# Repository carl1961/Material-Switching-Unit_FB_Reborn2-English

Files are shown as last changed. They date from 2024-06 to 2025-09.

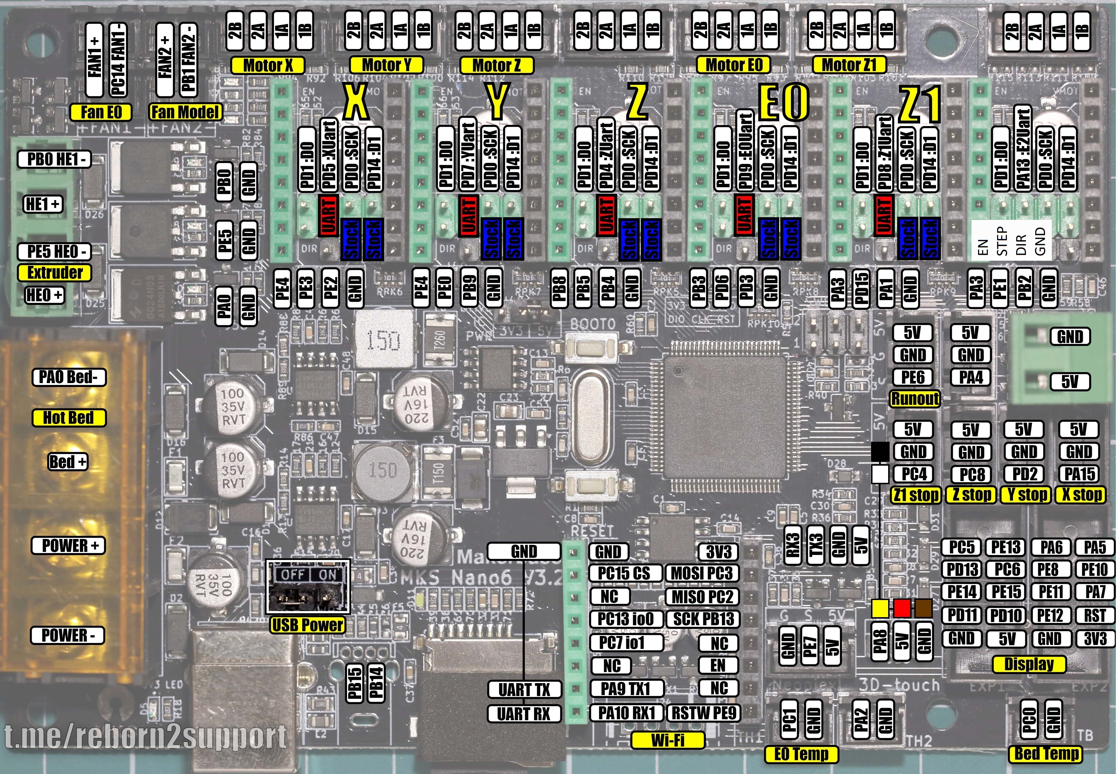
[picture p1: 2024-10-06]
MKS_Nano6_v3.2_PINOUT.jpg

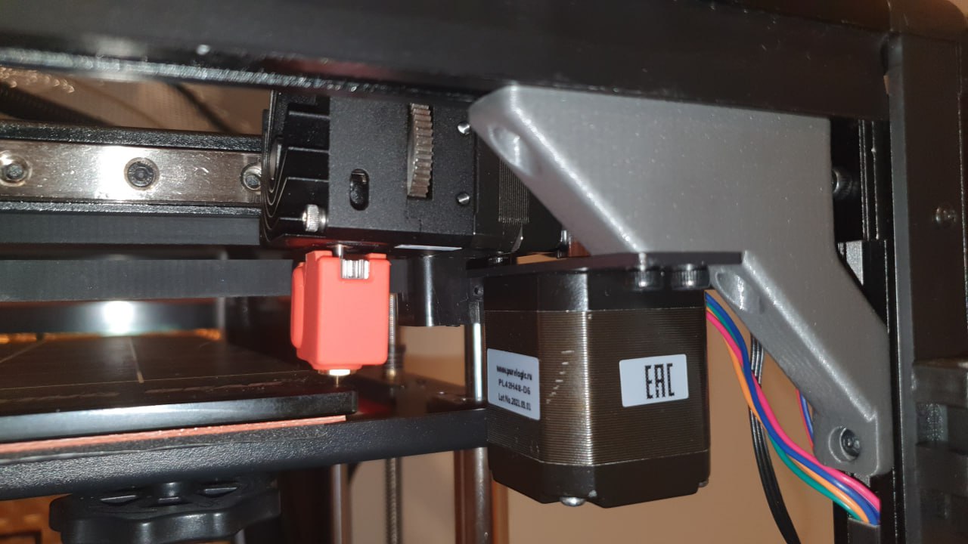
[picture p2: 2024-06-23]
parts/Reborn2/motor flip/photo_2023-03-01_20-06-13.jpg

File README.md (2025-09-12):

                

Filament replacement device for printing with various plastics and multi-color printing.

Modification for the printer **FlyingBear Reborn 2**.
A small guide and [overview](https://rozhkovets-home.ru/?p=464)

It can be discussed [here](https://t.me/+KcA09gXNElsxNDQy)

Initial condition of the equipment and modifications:
* BIQU H2 V2S extruder
* Blower model 1x5015
* Wi-Fi module removed
* Drivess X and Y are inverted
* Motherboard MKS Robin Nano 3.2 (STM32F407VET6)
* Display MKS mini 12864 V3.0
* Stepper motor driver - TMC 2209
* BLTouch sensor (UBL alignment 12x12)
* Parking Z by limit switches
* Print area  300x300x350mm 

In addition to [the list](https://github.com/rozhkovets/Material-Switching-Unit_FB_Reborn2/blob/main/Build_guide_MSU.md#parts-required) required equipment is needed:
  * another stepper motor driver
  * change the connection of the stepper motors (without this, the Z2 motor stops working during printing)
    * E0 -> E1
    * E1(Z2) -> E0
    * The stepper motor MSU is connected in E2. 
  * servo drive for the filament cutter, in case it is used
  * filament presence sensor (BTT SFS or similar) **(highly recommended)**

The servos are connected to the contacts:
   * PC3
   * PC2
   * It can be connected to others, but unstable operation is possible - flickering, turning at an incorrect angle..
____________________
1. Print the necessary [parts](https://github.com/rozhkovets/Material-Switching-Unit_FB_Reborn2/tree/main/parts/Reborn2) 
2. Gather
3. Connect the motors according to the table.

|Motor|  Original Port  | MCU |
| --- | --- | --- |
|  X |  X Motor | X Motor |
|  Y |  Y Motor | Y Motor |
|  Z1  | Z1 Motor | Z1 Motor |
|  E0 | E0 Motor | E1-motor |
|  Z2 | E1 Motor| E0-motor |
|  MSU E | | E2 Motor |

4. Compile the firmware with the necessary settings and install the firmware..
5. Be prepared for problems

**Frequent problems:**
  * The MSU motor cannot push the filament - Increase or decrease the pressure. A large current for the motor is not required. It would be better if the motor starts skipping steps when it gets stuck, rather than grinding the filament.
  * The filament gets stuck in the splitter when entering the ptfe tube - Deburr the entrance to the ptfe tube with a knife. Slightly twist or remove the tube from the splitter. Change the angle of cutting the filament.
  * The filament gets stuck when entering the fitting - Use another fitting. Change the angle of the filament cut.
  *The filament gets stuck in the BTT SFS filament motion sensor - Change the cutting angle of the filament. Change the angle of the filament entering the sensor channel. Ream the output channel from 2 to 3 mm, create a small chamfer at the entrance to the channel. Suffer.
  * The filament gets stuck at the entrance to the cutter - enlarge the hole with a drill. Shift the filament motion sensor sideways by inserting washers. (Shifting it by 1 mm was enough for me). Change the angle of the filament cutting. Change the angle of the filament entry.
  * The filament is not being cut by the cutter - Replace the blade. Increase the number of cutting attempts.
  * The filament gets stuck at the entrance of the extruder - Change the filament cutting angle. Upgrade your biqu h2 v2 by installing a ptfe tube between the gears to reduce gaps, [instructions](https://m.youtube.com/watch?v=L_tcQAx7UfE).
____________________

# Material Switching Unit (MSU)

The Material Switching Unit is a multi-material upgrade for 3D printers based on the MMU2 that allows printing of up to 5 filaments while staying under 80$ and being compatible with most FDM 3D printers out there.

# Getting started

Once this is done you should now have access to the different parts required for this project. The Marlin folder contains the modified firmware that will allow you to control the MSU and the parts forlder contains all the 3D files that you will need.

have a look at the [build guide](https://github.com/PierreMasselot1/Material-Switching-Unit/blob/main/Build_guide_MSU.md) for further guidance on how to get the MSU up and running!

# Goals

* The MSU is currently still a prototype, improving reliability is currentlyy the main goal. The main focus being at the Slicer level ([here](https://github.com/PierreMasselot1/SuperSlicer) is the fork that I am working on) but also some improvements that can still be done to the actual device.

* Presets and profiles! Not having the tweak the MSU for hours will make the barrier to entry much lower

# Notes

The main barrier I have right now is time, juggling everything from uni and career to friends and sports does take quite a bit of time so if you see that this repo hasn't been updated in a while it's not because the project is dead ;) it's just that I haven't had the time to work on it.

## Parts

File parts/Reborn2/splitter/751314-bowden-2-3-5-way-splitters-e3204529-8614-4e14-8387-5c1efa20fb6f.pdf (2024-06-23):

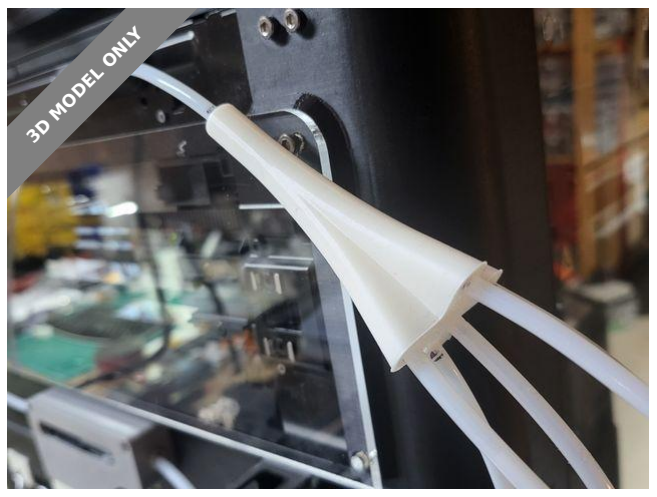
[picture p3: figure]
3D MODEL ONLY

## Summary

Split your bowden tube

3D Printers (https://printables.com/model?categoryId=1) | > | Other Printer Parts & Upgrades (https://printables.com/model?categoryId=2)
Tags: | multicolor | ptfe | bowden | splitter | ams

After many, many iterations I finally have a splitter I'm happy with. I

primarily designed it as a 5 way splitter but it's mostly parametric so I was

able to produce 2 and 3 way versions. 4, 6 and maybe 7 way splitters may

be possible with a bit more tweaking, if there's interest let me know.

Here are the main features I aimed for:

Angled inlets to minimize the number of curves the filament has to go

## through

Built in PTFE connectors that do not reduce the diameter or deform

the inside of the PTFE tube

Prints without support

Here are the printing / installation instructions (PLEASE READ BEFORE

### USING):

Print upright and use the smallest layer hight your printer is capable

of. I printed mine at .16mm

If you have adhesion issues print with an outside brim

TLA (https://printables.com/@TLA_209275)

## Bowden 2-3-5 Way

# Splitters

### VIEW IN BROWSER (https://printables.com/model/751314-bowden-2-3-5-way-splitters)

updated 5. 2. 2024 | published 5. 2. 2024

•

•

•

•

•

# Model files

This splitter is designed for PTFE tubes with 4mm OD and 2mm ID

To make installation easier, each PTFE tube needs to have a thread

cut into it

For all tubes, make sure they are all cut square, and the openings are

round, not squished, otherwise you'll have problems

Using tape or a marker, from the end measure 15 mm for the outlet

PTFE tube and 17mm for each of the inlet PTFE tubes

Use the bottom, middle opening as a die to cut the thread into the

PTFE tubes, use light force to push the PTFE tube as you turn it in, it

should go in as far as the marking you made, 5 or 6 full turns should

## do it

If you have trouble gripping the PTFE tube try wrapping it with

masking tape

Since the tubes are turned into place it's best if the other ends are

unplugged during assembly

Install the top tube until it bottoms out which is about 15mm

Install the bottom tubes until you reach 17.5mm or until you feel it

### bottoming out. ONCE YOU DETECT THE BOTTOM DO NOT TIGHTEN

ANY FURTHER. This is because the channel is tapered and it will

squish the PTFE tube inward causing unwanted friction

Test each filament path once assembled, you may need to screw in/

out some of the PTFE tube as needed.

That's it, let me know if these work for you or not.

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
bowden⁻5-way-splitter.stl

bowden⁻3-way-splitter.stl

bowden⁻2-way-splitter.stl

## License

This work is licensed under a

Creative Commons (4.0 International License)

Attribution—Noncommercial—Share Alike (http://creativecommons.org/licenses/by-nc-sa/4.0/)

### ✖ | Sharing without ATTRIBUTION

✔ | Remix Culture allowed
✖ | Commercial Use
✖ | Free Cultural Works
✖ | Meets Open Definition

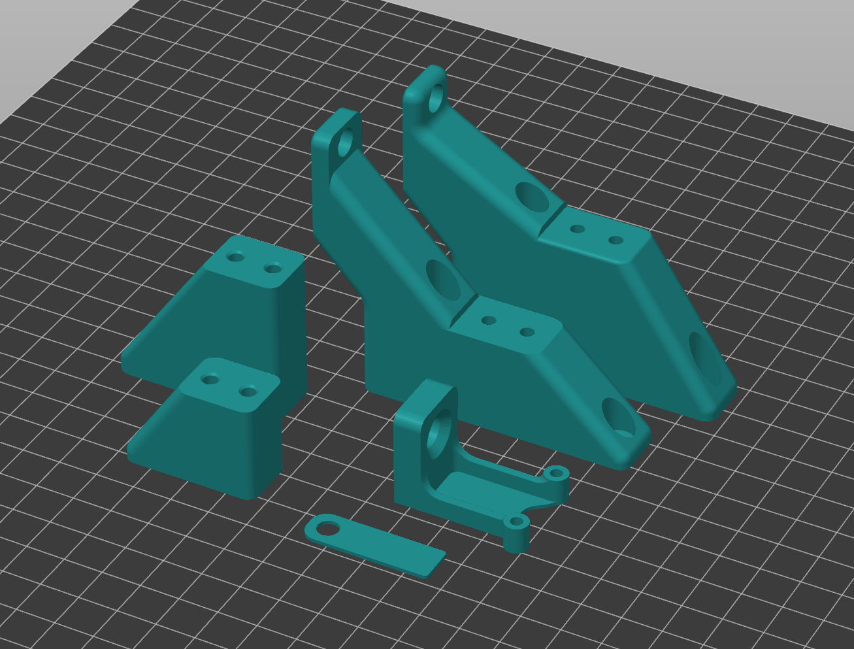
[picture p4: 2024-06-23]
parts/Reborn2/motor flip/view.png

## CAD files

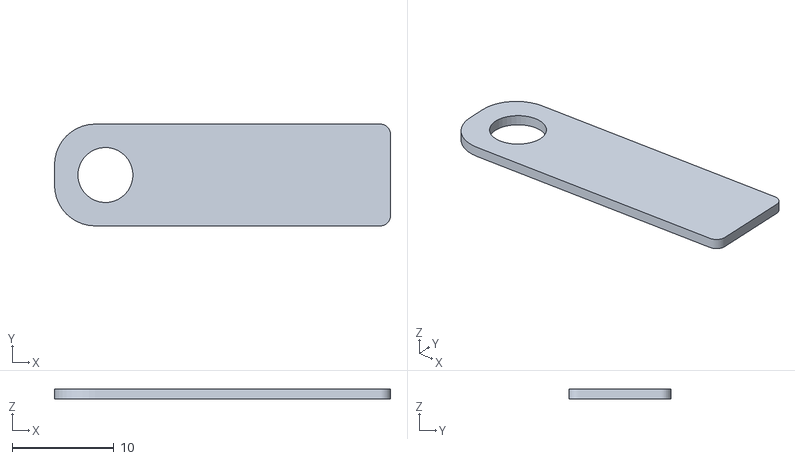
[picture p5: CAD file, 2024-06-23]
parts/Reborn2/motor flip/end1.STL
33.0 x 10.0 x 1.00

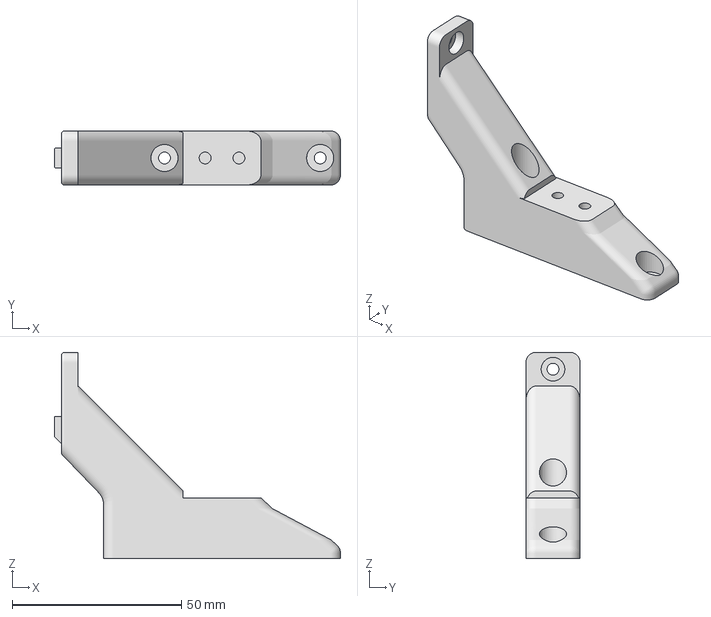
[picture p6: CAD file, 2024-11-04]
parts/Reborn2/motor flip/motor leadshine/7-right-front.3mf
84.5 x 16.0 x 61.0 mm

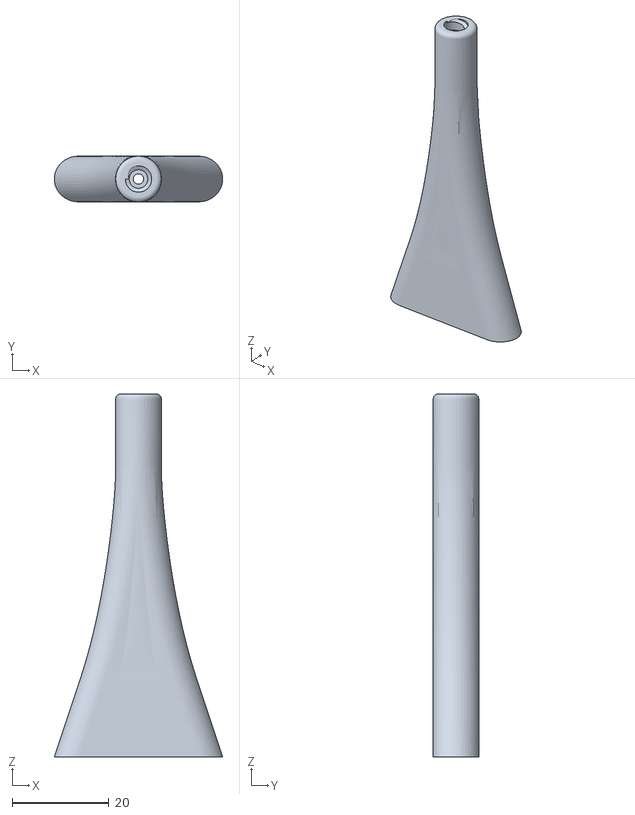
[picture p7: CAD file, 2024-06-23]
parts/Reborn2/splitter/bowden-3-way-splitter.stl
34.8 x 9.45 x 75.0

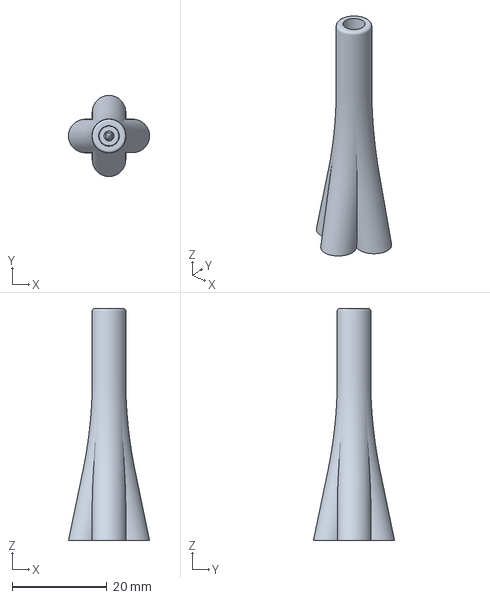
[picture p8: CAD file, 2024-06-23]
parts/Reborn2/splitter/прочие/Y-Splitter+v9改5通道.3mf
17.1 x 17.2 x 49.0 mm

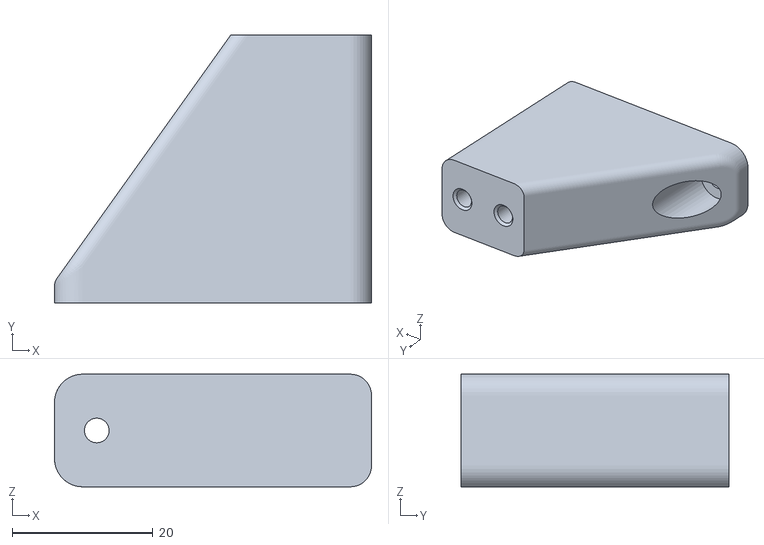
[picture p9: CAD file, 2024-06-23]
parts/Reborn2/motor flip/left-side.STL
45.0 x 38.0 x 16.0

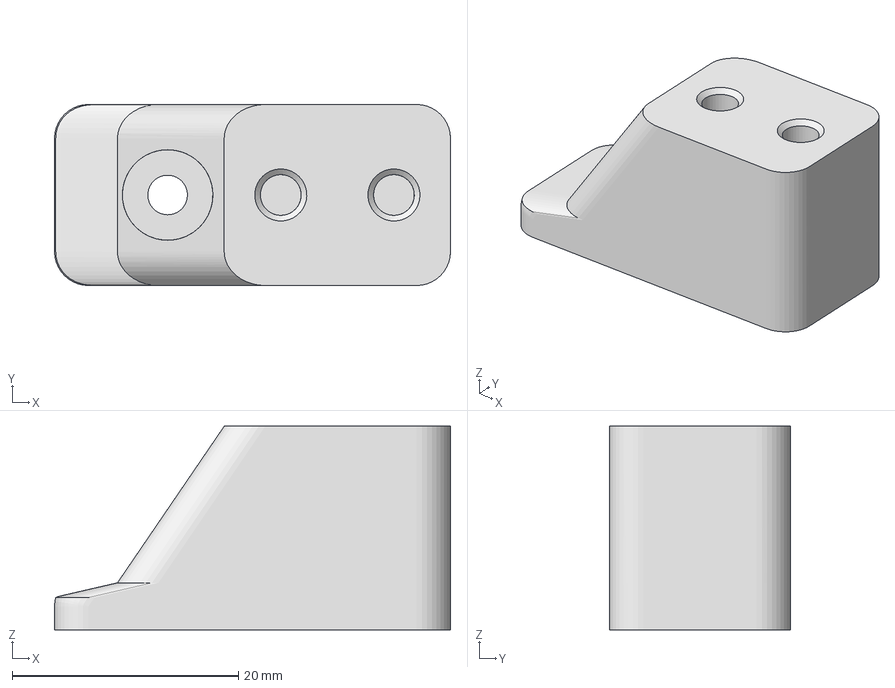
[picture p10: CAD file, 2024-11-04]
parts/Reborn2/motor flip/motor leadshine/7-right-side.3mf
35.0 x 16.0 x 18.0 mm

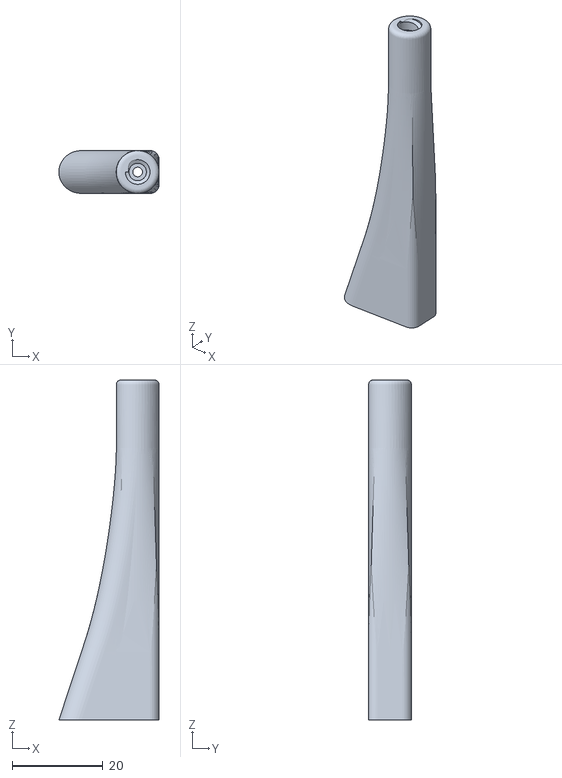
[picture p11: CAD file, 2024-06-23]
parts/Reborn2/splitter/bowden-2-way-splitter.stl
22.1 x 9.45 x 75.0

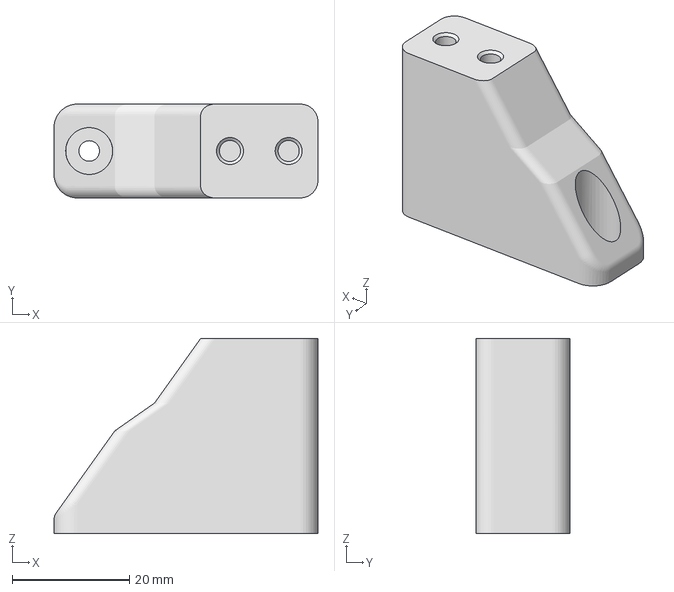
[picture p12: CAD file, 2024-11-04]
parts/Reborn2/motor flip/motor leadshine/33,25-left-side.3mf
45.0 x 16.0 x 33.2 mm

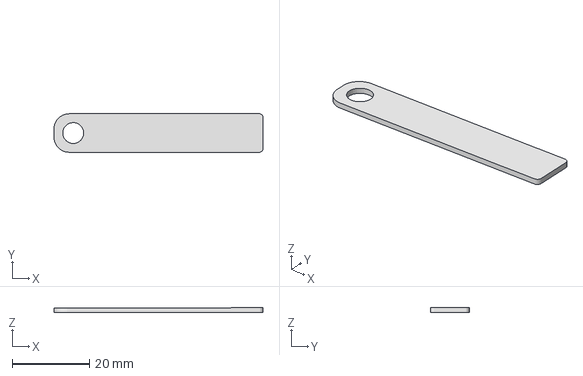
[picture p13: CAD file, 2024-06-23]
parts/Reborn2/motor flip/длинный флажок Y end 1.3mf
54.1 x 9.98 x 1.20 mm

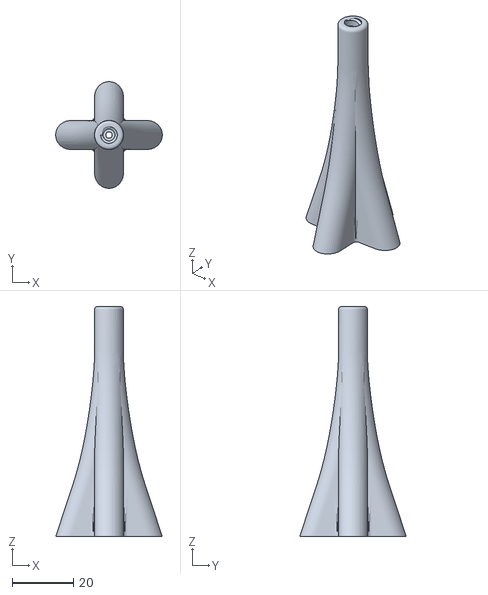
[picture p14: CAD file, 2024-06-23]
parts/Reborn2/splitter/bowden-5-way-splitter.stl
34.8 x 34.8 x 75.0

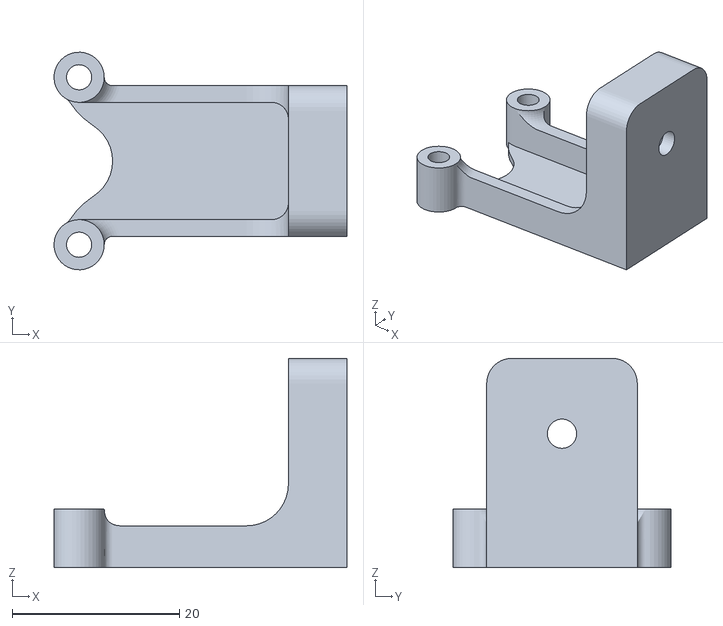
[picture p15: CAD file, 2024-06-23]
parts/Reborn2/motor flip/end2.STL
35.0 x 26.0 x 25.0

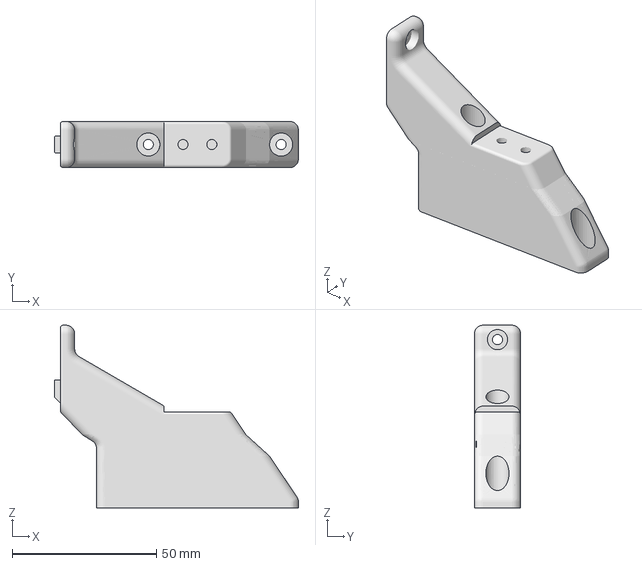
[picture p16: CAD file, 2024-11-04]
parts/Reborn2/motor flip/motor leadshine/33,25-left-front.3mf
84.5 x 16.0 x 63.2 mm

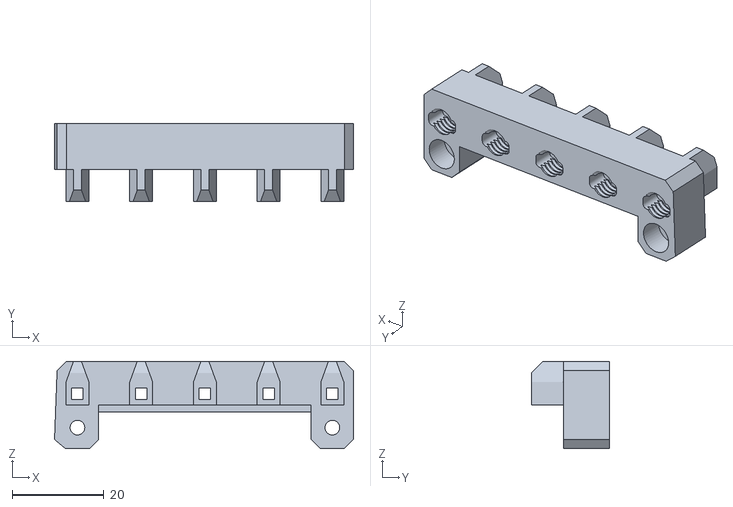
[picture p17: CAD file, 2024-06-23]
parts/Reborn2/splitter/adapter.stl
65.1 x 17.0 x 19.0

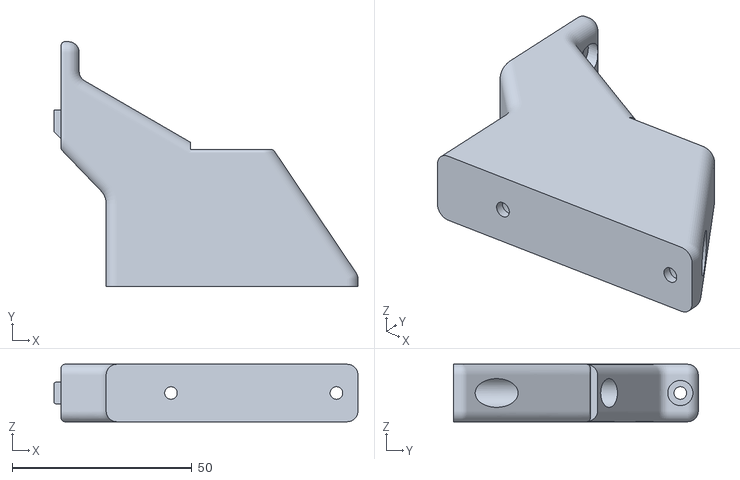
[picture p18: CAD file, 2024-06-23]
parts/Reborn2/motor flip/left-front.STL
84.5 x 68.0 x 16.0

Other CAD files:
parts/Reborn2/motor flip/right-side.STL
parts/Reborn2/motor flip/right-front.STL

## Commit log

2024-06-22 Update README.md
    Добавлено описание для Reborn 2
2024-06-23 STEP upload
    [Y-Splitter+v9改5通道.3mf, adapter.stl, bowden-2-way-splitter.stl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]
2024-10-06 submodule "Marlin-MSU"
2024-11-04 Parts for Reborn 2 update
    [33,25-left-front.3mf, 33,25-left-side.3mf, 7-right-front.3mf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]
2024-12-21 NF Sunrise
    mount for Mellow NF Sunrise extruder with bl touch, 4010 fan, servo cutter, nozzle wiper
2025-01-13 Update Marlin-MSU
2025-02-09 marlin update
2025-04-19 Update Marlin to bugfix 2.1.x 26b3f0b (19.04.25)
2025-06-22 module update to Marlin-bugfix-2.1.x-83af0e6(22.06.25)
